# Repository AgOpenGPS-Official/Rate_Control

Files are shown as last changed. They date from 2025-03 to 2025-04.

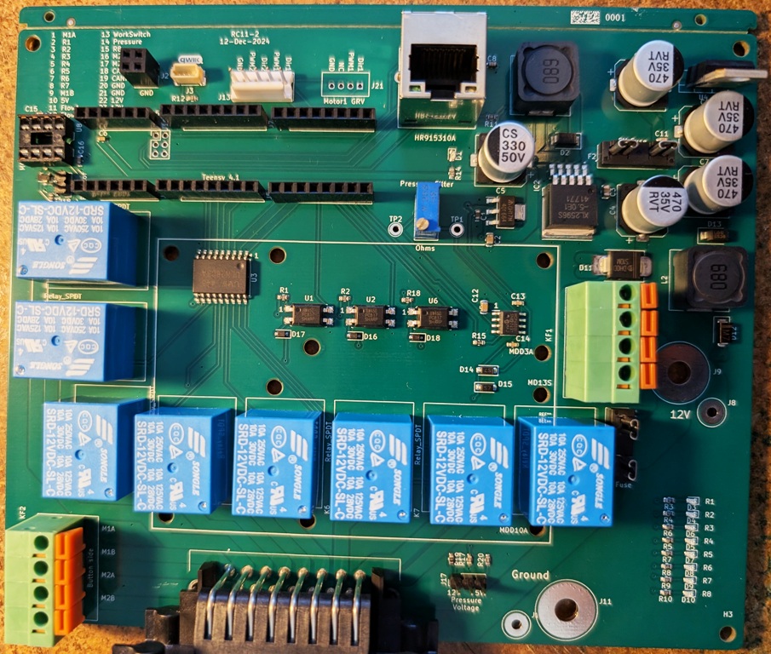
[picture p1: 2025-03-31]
Teensy/RC11-2/Bare board.jpg

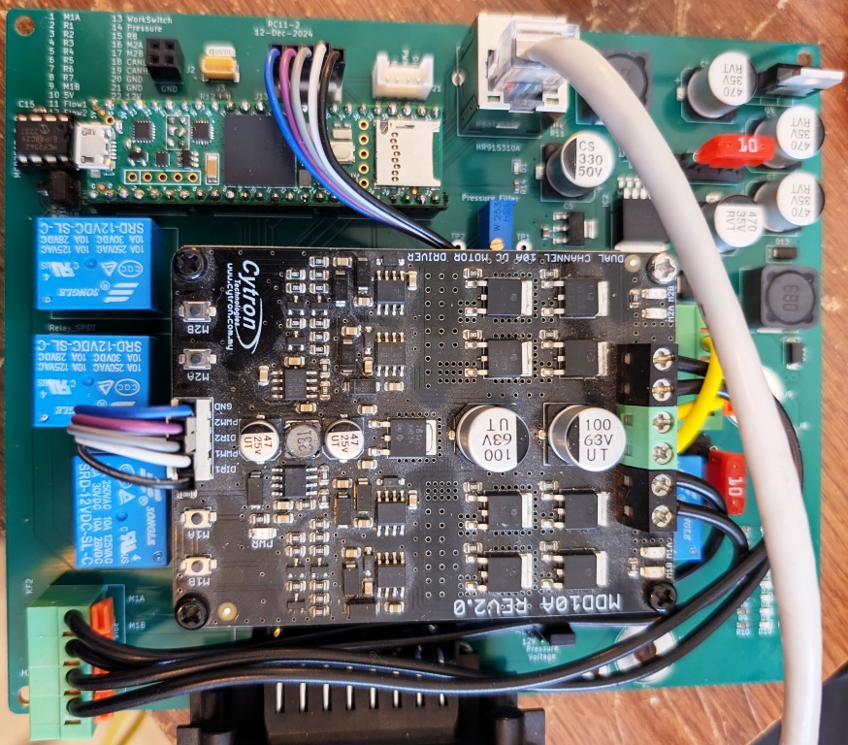
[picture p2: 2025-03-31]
Teensy/RC11-2/Dual motor drive.jpg

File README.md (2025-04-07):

### [Nano RC12-3](Nano/RC12-3)
- uses a Nano (with ENC28J60 Ethernet shield) & an on-board mounted Cytron for rate control
	- 1 or 2 [MD13S](https://www.cytron.io/p-13amp-6v-30v-dc-motor-driver) for rate control
- self assembled through-hole board, least expensive
- controls two rates
- can be connected to a relay module with a 20 pin cable or dupont connectors
- work switch
- pressure switch
- [OSHPARK]([https://oshpark.com/shared_projects/UU8e90h9](https://oshpark.com/shared_projects/fRBlR1Se)
RC12-3

#
### [Teensy 4.1 RC11-2](Teensy/RC11-2_PCB)
- uses a Teensy & an on-board mounted Cytron for rate control
	- either (1) [MD13S](https://www.cytron.io/p-13amp-6v-30v-dc-motor-driver) for single rate control
 	- or (1) [MDD10A](https://www.cytron.io/p-10amp-5v-30v-dc-motor-driver-2-channels) for dual rate control
- small components are surface mount parts
- Teensy Ethernet 
- can control two rates and eight sections
	- 8 relays (SPDT 12V output)
	- (1) 5V or 12V analog (pressure) input, potentiometer adjustable filtering
	- (2) optically isolated digital (rate/pulse) inputs (5V or 12V)
- 3.3V I2C headers (Qwiic)
	- supports optional external RelayDriver5 I2C board
 - work switch
 - canbus
RC11-2

#
### [ESP32 RC15](ESP32/RC15)
- uses an ESP32 (optional W5500 Ethernet Module)
- mostly surface mount parts
- can control two rates and 7-14 sections
	- (2) DRV8870 motor drivers with reversible outputs for rates
	- (7) DRV8870 motor drivers for either 7 reversible (motorized ball valve) outputs or 14 single ended (high or low) section outputs
- (4) 5V analog inputs (or 2 differential inputs)
- (2) optically isolated digital (rate/pulse) inputs, up to 12V
- RS485 chip & header
- 3.3V I2C header
	- supports optional external RelayDriver5 I2C board
ESP32-RC15

#
### [RelayDriver5](RelayDriver5)
- PCA9535 based I2C IO expander
- designed to plug into 8 or 16 channel relay board with Qwiic cable
RelayDriver5 photo
#
### Firmware
https://github.com/SK21/AOG_RC

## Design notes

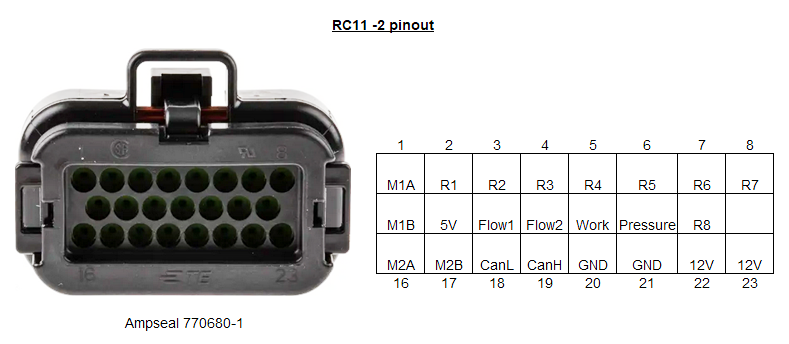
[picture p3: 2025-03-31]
Teensy/RC11-2/RC11-2 PinOut.PNG

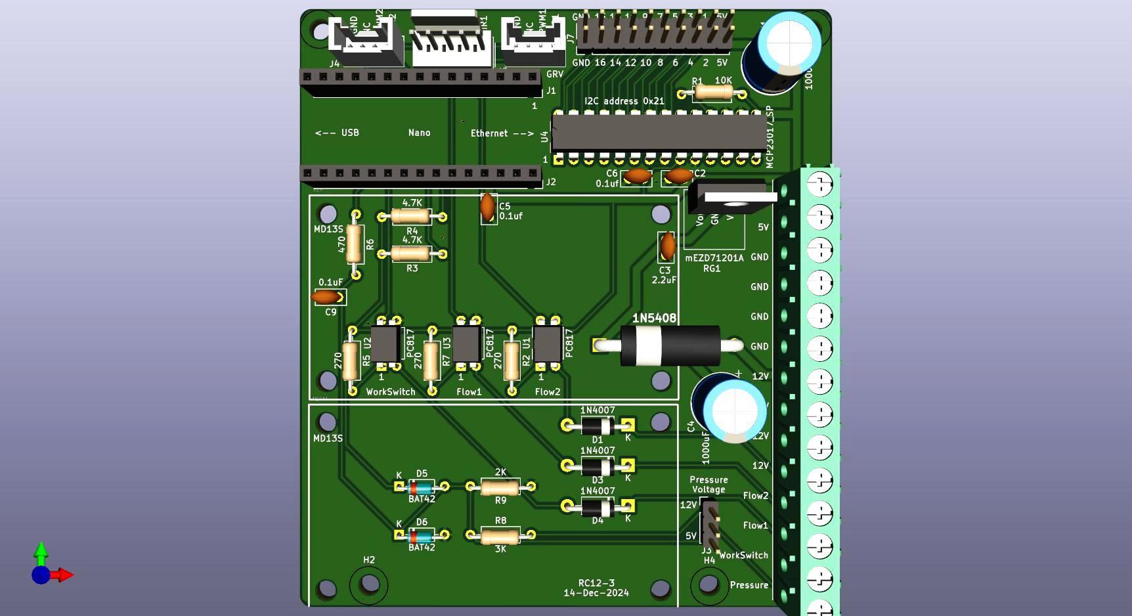
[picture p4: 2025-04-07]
Nano/RC12-3/RC12-3.jpg

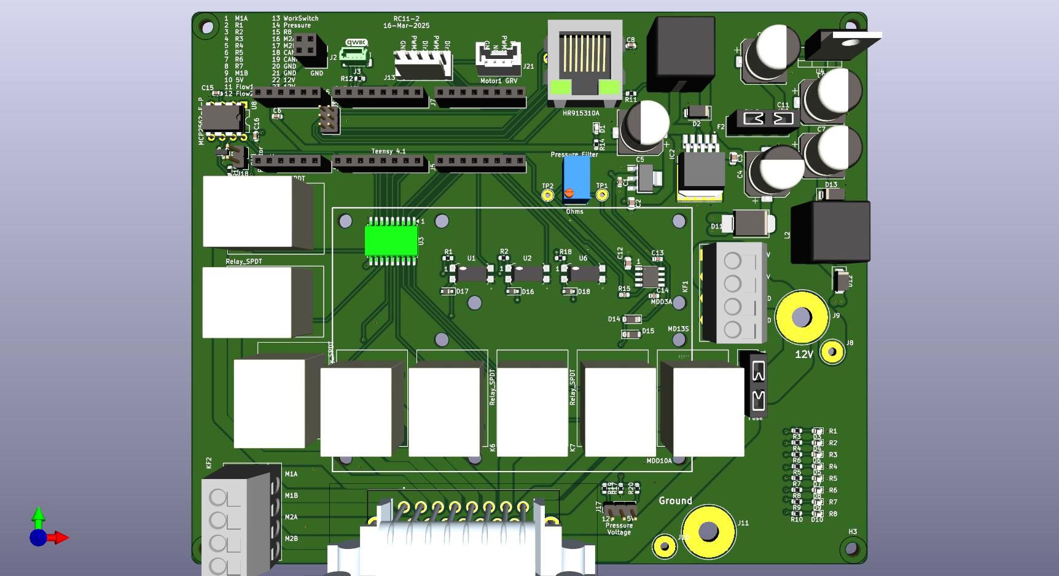
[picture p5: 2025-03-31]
Teensy/RC11-2/PCB/RC11-2.jpg

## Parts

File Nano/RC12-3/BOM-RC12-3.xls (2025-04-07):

Item # | Comment | Designator | Footprint | Quantity
1 | 1000uF | C1, C4 | CP_Radial_D10.0mm_P5.00mm | 2
2 | 10uF | C2 | C_Disc_D5.0mm_W2.5mm_P2.50mm | 1
3 | 2.2uF | C3 | C_Disc_D5.0mm_W2.5mm_P2.50mm | 1
4 | 0.1uf | C5, C6, C9 | C_Disc_D5.0mm_W2.5mm_P2.50mm | 3
5 | 1N4007 | D1, D3, D4 | D_DO-41_SOD81_P10.16mm_Horizontal | 3
6 | 1N5408 | D2 | 1N5408 | 1
7 | BAT42 | D5, D6 | D_DO-35_SOD27_P7.62mm_Horizontal | 2
8 | Conn_01x15_Female | J1, J2 | PinSocket_1x15_P2.54mm_Vertical | 2
9 | Pressure | J3 | PinHeader_1x03_P2.54mm_Vertical | 1
10 | Motor2 GRV | J4, J5 | Grove | 2
11 | Screw_Terminal_01x14 | J6 | TerminalBlock_Phoenix_PT-1,5-14-5.0-H_1x14_P5.00mm_Horizontal | 1
12 | Relay | J7 | PinHeader_2x10_P2.54mm_Vertical | 1
13 | Conn_01x05 | J9 | Molex_KK-254_AE-6410-05A_1x05_P2.54mm_Vertical | 1
14 | 10K | R1 | R_Axial_DIN0207_L6.3mm_D2.5mm_P10.16mm_Horizontal | 1
15 | 270 | R2, R5, R7 | R_Axial_DIN0207_L6.3mm_D2.5mm_P10.16mm_Horizontal | 3
16 | 4.7K | R3, R4 | R_Axial_DIN0207_L6.3mm_D2.5mm_P10.16mm_Horizontal | 2
17 | 470 | R6 | R_Axial_DIN0207_L6.3mm_D2.5mm_P10.16mm_Horizontal | 1
18 | 3K | R8 | R_Axial_DIN0207_L6.3mm_D2.5mm_P10.16mm_Horizontal | 1
19 | 2K | R9 | R_Axial_DIN0207_L6.3mm_D2.5mm_P10.16mm_Horizontal | 1
20 | mEZD71201A | RG1 | mEZD71201A | 1 | https://www.universal-solder.ca/product/dc-dc-buck-converter-5v-1a-7805-replacement/
21 | PC817 | U1, U2, U3 | DIP-4_W7.62mm | 3
22 | MCP23017_SP | U4 | DIP-28_W7.62mm | 1
23 | Nano |  |  | 1
24 | MD13S |  |  | 2
25 | IDC 20 pin flat ribbon cable |  |  | 1 | https://www.amazon.ca/Ribbon-Cable-Connector-2-54mm-Length/dp/B07T3VH9Y7
26 | 8 or 16 relay module |  |  | 1 | https://www.amazon.ca/ELEGOO-Channel-Optocoupler-Arduino-Raspberry/dp/B06XCN5JNH
27 | M3 standoffs |  |  | 4 | https://www.amazon.ca/Lystaii-Standoff-Motherboard-Standoffs-Assortment/dp/B08LPYR49C
 | RC12-3
 | Mouser # | Mfr. # | Manufacturer |  | Description | Order Qty. | Price (CAD) | Ext.: (CAD)
1 | 667-EEU-FR1E102B | EEU-FR1E102B | Panasonic |  | Aluminum Electrolytic Capacitors - Radial Leaded 25VDC 1000uF 10x20mm LS | 2 | $1.61 | $3.22
2 | 810-FA20X7S1H106KRU6 | FA20X7S1H106KRU06 | TDK |  | Multilayer Ceramic Capacitors MLCC - Leaded 50V 10uF X7S 10% RAD LS:5mm AEC-Q200 | 1 | $1.65 | $1.65
3 | 810-FG18X5R1E225KRT6 | FG18X5R1E225KRT06 | TDK |  | Multilayer Ceramic Capacitors MLCC - Leaded RAD 25V 2.2uF X5R 10% LS:2.5mm | 1 | $0.435 | $0.44
4 | 594-K104K10X7RF5UH5 | K104K10X7RF5UH5 | Vishay |  | Multilayer Ceramic Capacitors MLCC - Leaded 0.1uF 50volt 10% 5.0mm X7R | 3 | $0.261 | $0.78
5 | 637-1N4007 | 1N4007 | Diotec Semiconductor |  | Rectifiers Diode, DO-41, 1000V, 1A | 3 | $0.145 | $0.44
6 | 625-1N5408-E3 | 1N5408-E3/54 | Vishay |  | Rectifiers 3.0 Amp 1000 Volt | 1 | $0.769 | $0.77
7 | 625-BAT42 | BAT42-TR | Vishay |  | Schottky Diodes & Rectifiers 10mA 30 Volt | 2 | $0.247 | $0.49
8 | 200-SSW11501TMS | SSW-115-01-TM-S | Samtec |  | Headers & Wire Housings Tiger Buy Socket Strip with PCB Tails, .100" Pitch | 2 | $2.47 | $4.94
9 | 737-PH1-03-UA | PH1-03-UA | Adam Tech |  | Headers & Wire Housings CONN HEADER VERT 3POS 2.54MM | 1 | $0.145 | $0.15
11 | 651-1935284 | 1935284 | Phoenix Contact |  | Fixed Terminal Blocks PT 1.5/14-5.0-H | 1 | $4.29 | $4.29
12 | 737-PH2-10-UA | PH2-10-UA | Adam Tech |  | Headers & Wire Housings 10P AU FLASH SINGLE ROW STRAIGHT | 1 | $0.218 | $0.22
13 | 538-171856-0005 | 171856-0005 | Molex |  | Headers & Wire Housings KK Hdr Vrt 5 Ckt 2.54mm Pitch Sn | 1 | $0.493 | $0.49
14 | 603-CFR-12JR-5210K | CFR-12JR-52-10K | YAGEO |  | Carbon Film Resistors - Through Hole 10K ohm 1/6W 5% | 1 | $0.145 | $0.15
15 | 603-CFR-25JT-52-270R | CFR-25JT-52-270R | YAGEO |  | Carbon Film Resistors - Through Hole 1/4W 270 Ohm 5% | 3 | $0.145 | $0.44
16 | 279-CFR25J4K7 | CFR25J4K7 | TE Connectivity |  | Carbon Film Resistors - Through Hole 4.7KOhm 1/3W 1200PPM | 2 | $0.145 | $0.29
17 | 603-CFR-50JR-52470R | CFR-50JR-52-470R | YAGEO |  | Carbon Film Resistors - Through Hole 470ohm 1/2W 5% | 1 | $0.145 | $0.15
18 | 603-CFR-25JT-52-3K | CFR-25JT-52-3K | YAGEO |  | Carbon Film Resistors - Through Hole 3 kOhms 1/4W 250 V 5% - 55 C+ 155 C Axial - 350 PPM / C, + 500 PPM / C AEC-Q200 | 1 | $0.145 | $0.15
19 | 708-CF14JT2K00 | CF14JT2K00 | SEI Stackpole |  | Carbon Film Resistors - Through Hole 2KOhms 1/4W 5% Std Carbon | 1 | $0.145 | $0.15
21 | 852-PC817X3NSZ9F | PC817X3NSZ9F | Sharp Microelectronics |  | Transistor Output Optocouplers | 3 | $0.522 | $1.57
22 | 579-MCP23017-E/SP | MCP23017-E/SP | Microchip |  | Interface - I/O Expanders 16bit Input/Output Exp I2C interface | 1 | $2.45 | $2.45
24 | 713-108070021 | 108070021 | Seeed Studio |  | Power Management IC Development Tools MD13S - Cytron 13Amp DC Motor Driver | 2 | $21.03 | $42.06

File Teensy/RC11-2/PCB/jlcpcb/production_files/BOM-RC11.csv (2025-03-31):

Comment | Designator | Footprint | LCSC | Quantity
AZ1117 | IC1 | SOT230P700X180-4N | C110474 | 1
27K | RV1 | Potentiometer | C118932 | 1
0.1uF | C11,C13,C14,C15,C16,C6,C8 | C_0603_1608Metric | C14663 | 7
PESD1CAN_215 C15771 | S1 | DIO_PESD1CAN_215 | C15771 | 1
10uF | C2 | C_0805_2012Metric | C15850 | 1
I2C-3V3 | J3 | Qwic_vertical | C160390 | 1
S10MC | D11 | D_SMC_larger_pads | C169472 | 1
1N5819 C191023 | D16,D17,D18 | 1N5819 | C191023 | 3
120 | R16 | R_0603_1608Metric | C22787 | 1
150 | R11 | R_0603_1608Metric | C22808 | 1
LED | D1,D10,D3,D4,D5,D6,D7,D8,D9 | LED_0603_1608Metric | C2286 | 9
270 | R1,R18,R2 | R_0603_1608Metric | C22966 | 3
2K | R17 | R_0603_1608Metric | C22975 | 1
470 | R15 | C_0603_1608Metric | C23179 | 1
500 | R14 | R_0603_1608Metric | C23193 | 1
750 | R10,R3,R4,R5,R6,R7,R8,R9 | R_0603_1608Metric | C23253 | 8
Conn_01x08_Female | J16,J5,J6,J7 | PinSocket_1x08_P2.54mm_Vertical | C27438 | 4
HR915310A | J14 | CONN8_HR91531_HAN | C2760326 | 1
5.2K | R19 | R_0603_1608Metric | C2828621 | 1
1uF | C12,C3 | C_0805_2012Metric | C28323 | 2
470uF | C10,C4,C7,C9 | CP_Elec_10x10.5 | C2836436 | 4
SS36 | D13,D2 | SMA(DO-214AC) | C2903825 | 2
1K | R20 | R_0603_1608Metric | C2907113 | 1
Pressure | J17 | PinHeader_1x03_P2.54mm_Vertical | C2937625 | 1
Conn_02x02_Counter_Clockwise | J2 | PinSocket_2x02_P2.54mm_Vertical | C2977590 | 1
Relay_SPDT | K1,K2,K3,K4,K5,K6,K7,K8 | Songle_SRD-05VDC-SL-C | C30431 | 8
MCP2562-E-P | U8 | DIP-8_W7.62mm | C305904 | 1
776087-1-776087-1 | J12 | 7760871 | C378893 | 1
Motor1 GRV | J21 | Grove | C403774 | 1
Conn_01x06_Female | J15,J4 | PinSocket_1x06_P2.54mm_Vertical | C40877 | 2
2.2K | R12,R13 | R_0603_1608Metric | C4190 | 2
KF142V-5.0-4P | KF1,KF2 | KF142V-5.08-4P | C475136 | 2
Can Resistor | J18 | PinHeader_1x02_P2.54mm_Vertical | C492401 | 1
C492610 | F1,F2 | Fuse_Holder_C492610 | C492610 | 2
330uF | C5 | CP_Elec_10x10.5 | C5162354 | 1
LM7805_TO220 | U4 | TO-220-3_Vertical | C5444281 | 1
BAT42 | D14,D15 | D_SOD-123 | C5805639 | 2
22uF | C1 | C_0603_1608Metric | C59461 | 1
PC817 C66405 | U1,U2,U6 | SMD-4_4.6x7.62mm_P2.54mm | C66405 | 3
1N4007 C727081 | D12 | SMA(DO-214AC) | C727081 | 1
MCP6002-xP | U5 | SOIC127P600X175-8N | C7377 | 1
XL2596 | IC2 | TO263-5L | C74190 | 1
ULN2803A | U3 | ULN2803A | C845537 | 1
Conn_01x05 | J13 | Molex_KK-254_AE-6410-05A_1x05_P2.54mm_Vertical | C86505 | 1
SMDRI127-680MT | L1,L2 | TMPA1265SP-101MN-D | C9907 | 2
12V | J8 | PowerPinSmall |  | 1
Ground | J11 | PowerPin |  | 1
12V | J9 | PowerPin |  | 1
Ground | J10 | PowerPinSmall |  | 1
Pressure Ohms1 | TP1 | TestPoint_THTPad_D2.5mm_Drill1.2mm |  | 1
Pressure Ohms2 | TP2 | TestPoint_THTPad_D2.5mm_Drill1.2mm |  | 1
Teensy_Ethernet | J1 | PinHeader_2x03_P2.00mm_Vertical |  | 1

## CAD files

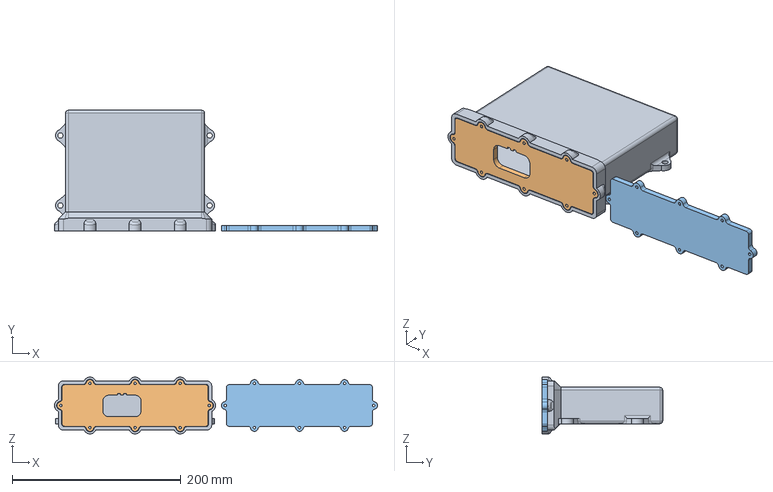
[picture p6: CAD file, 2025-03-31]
Teensy/RC11-2/Enclosure/RC11 box v7.step
383.1 x 143.0 x 67.4 mm

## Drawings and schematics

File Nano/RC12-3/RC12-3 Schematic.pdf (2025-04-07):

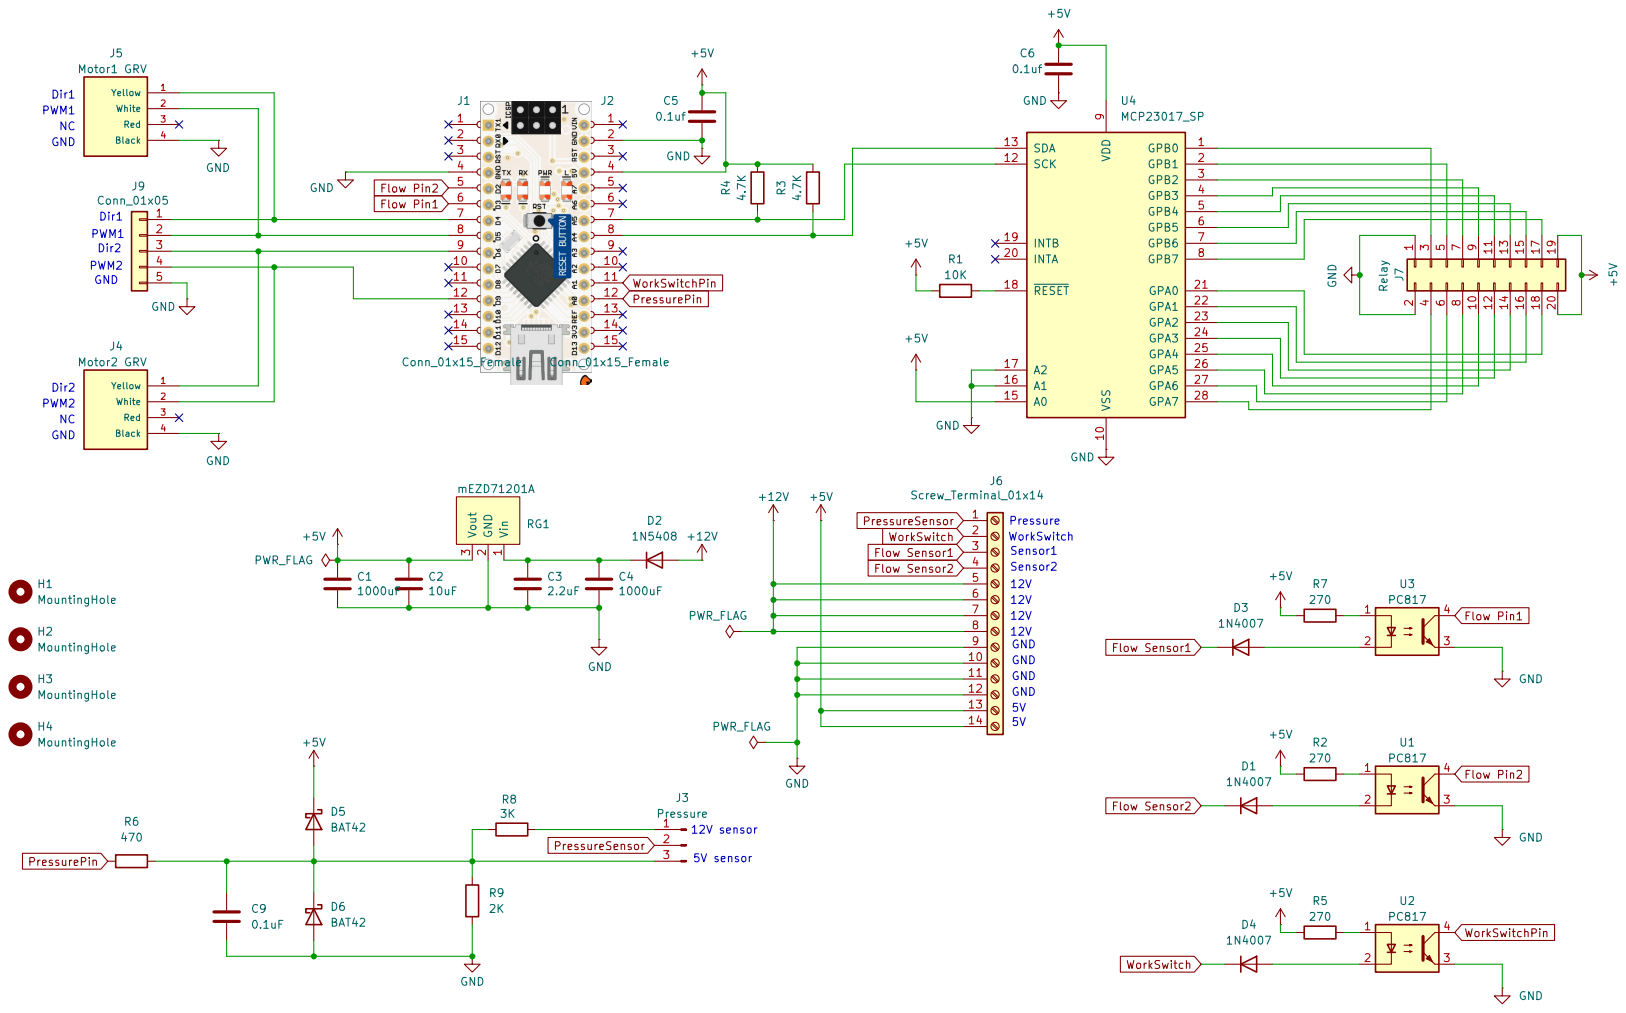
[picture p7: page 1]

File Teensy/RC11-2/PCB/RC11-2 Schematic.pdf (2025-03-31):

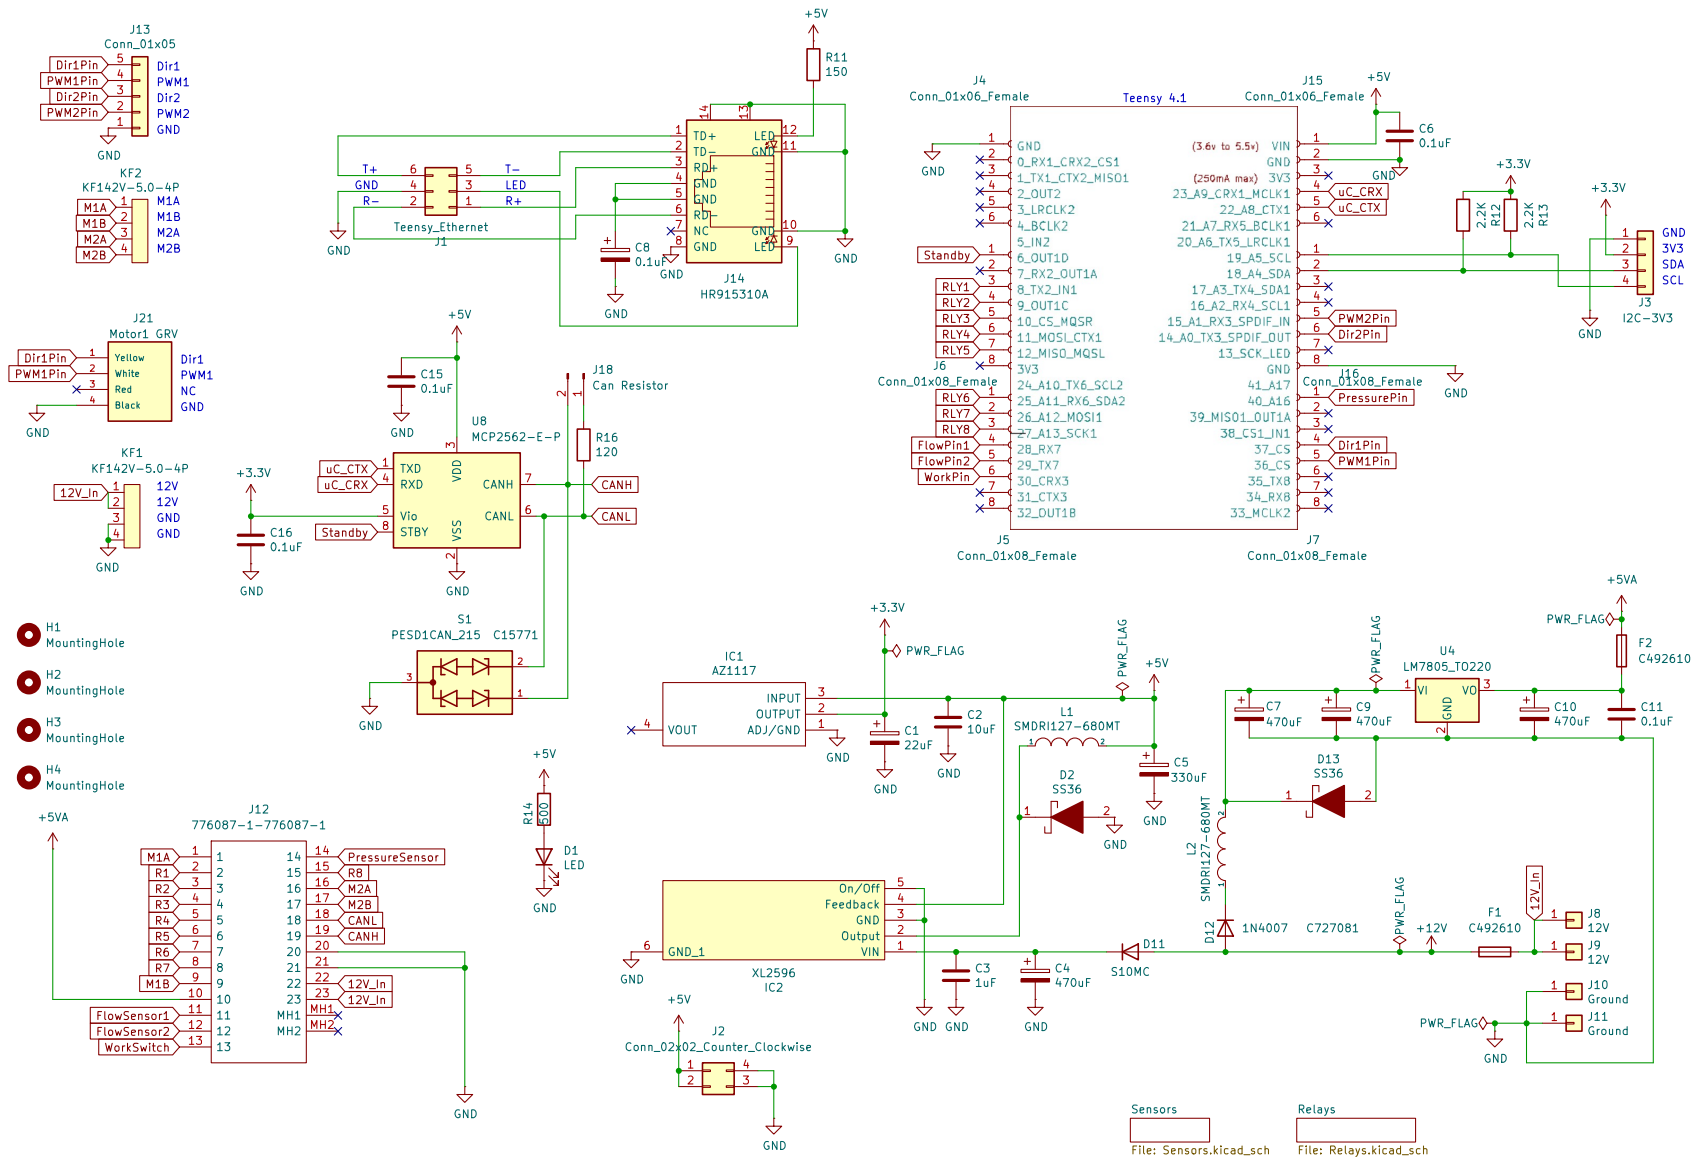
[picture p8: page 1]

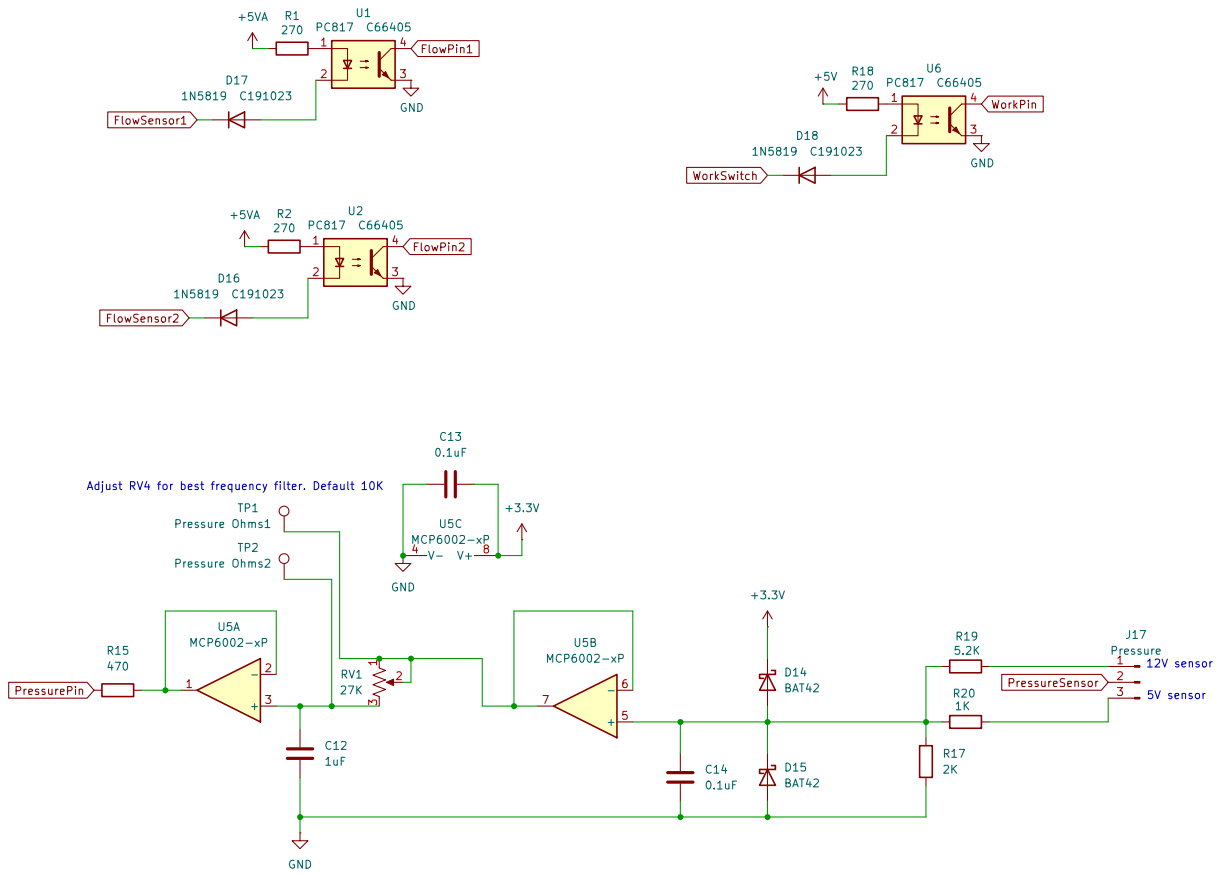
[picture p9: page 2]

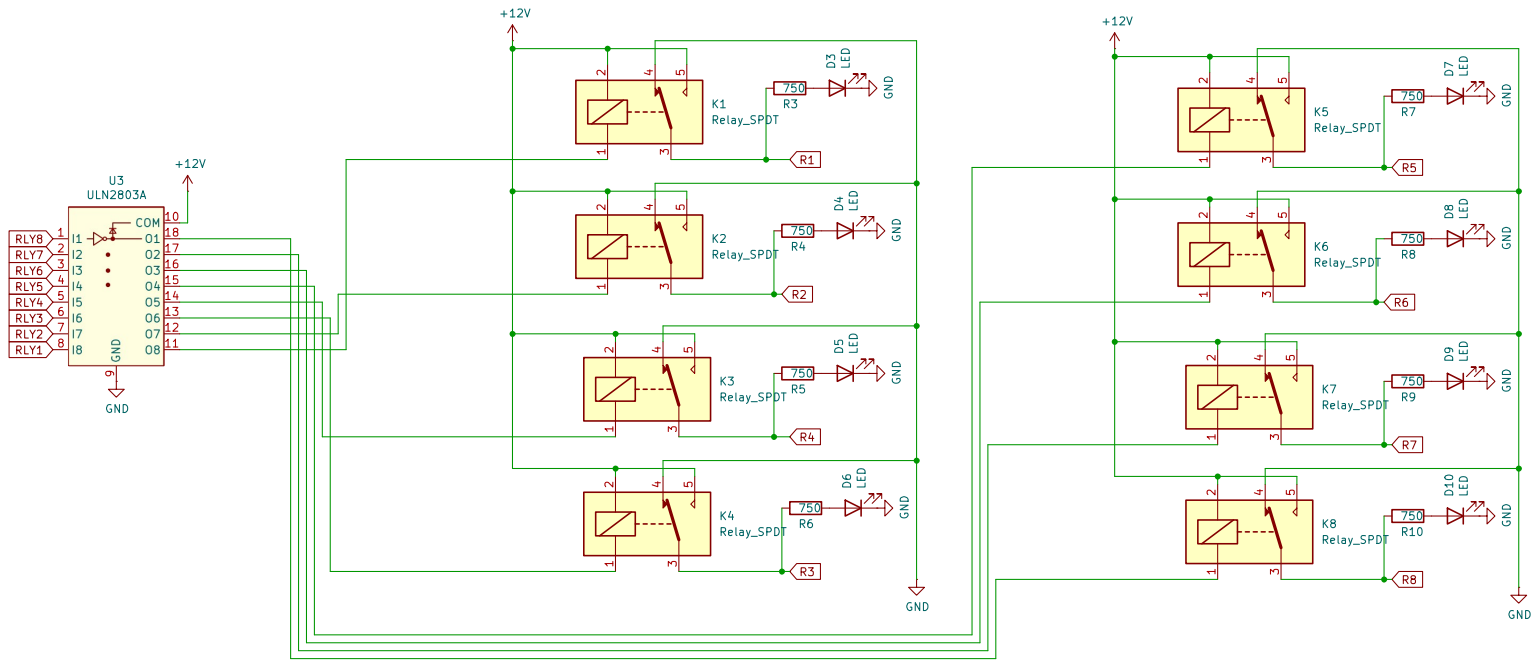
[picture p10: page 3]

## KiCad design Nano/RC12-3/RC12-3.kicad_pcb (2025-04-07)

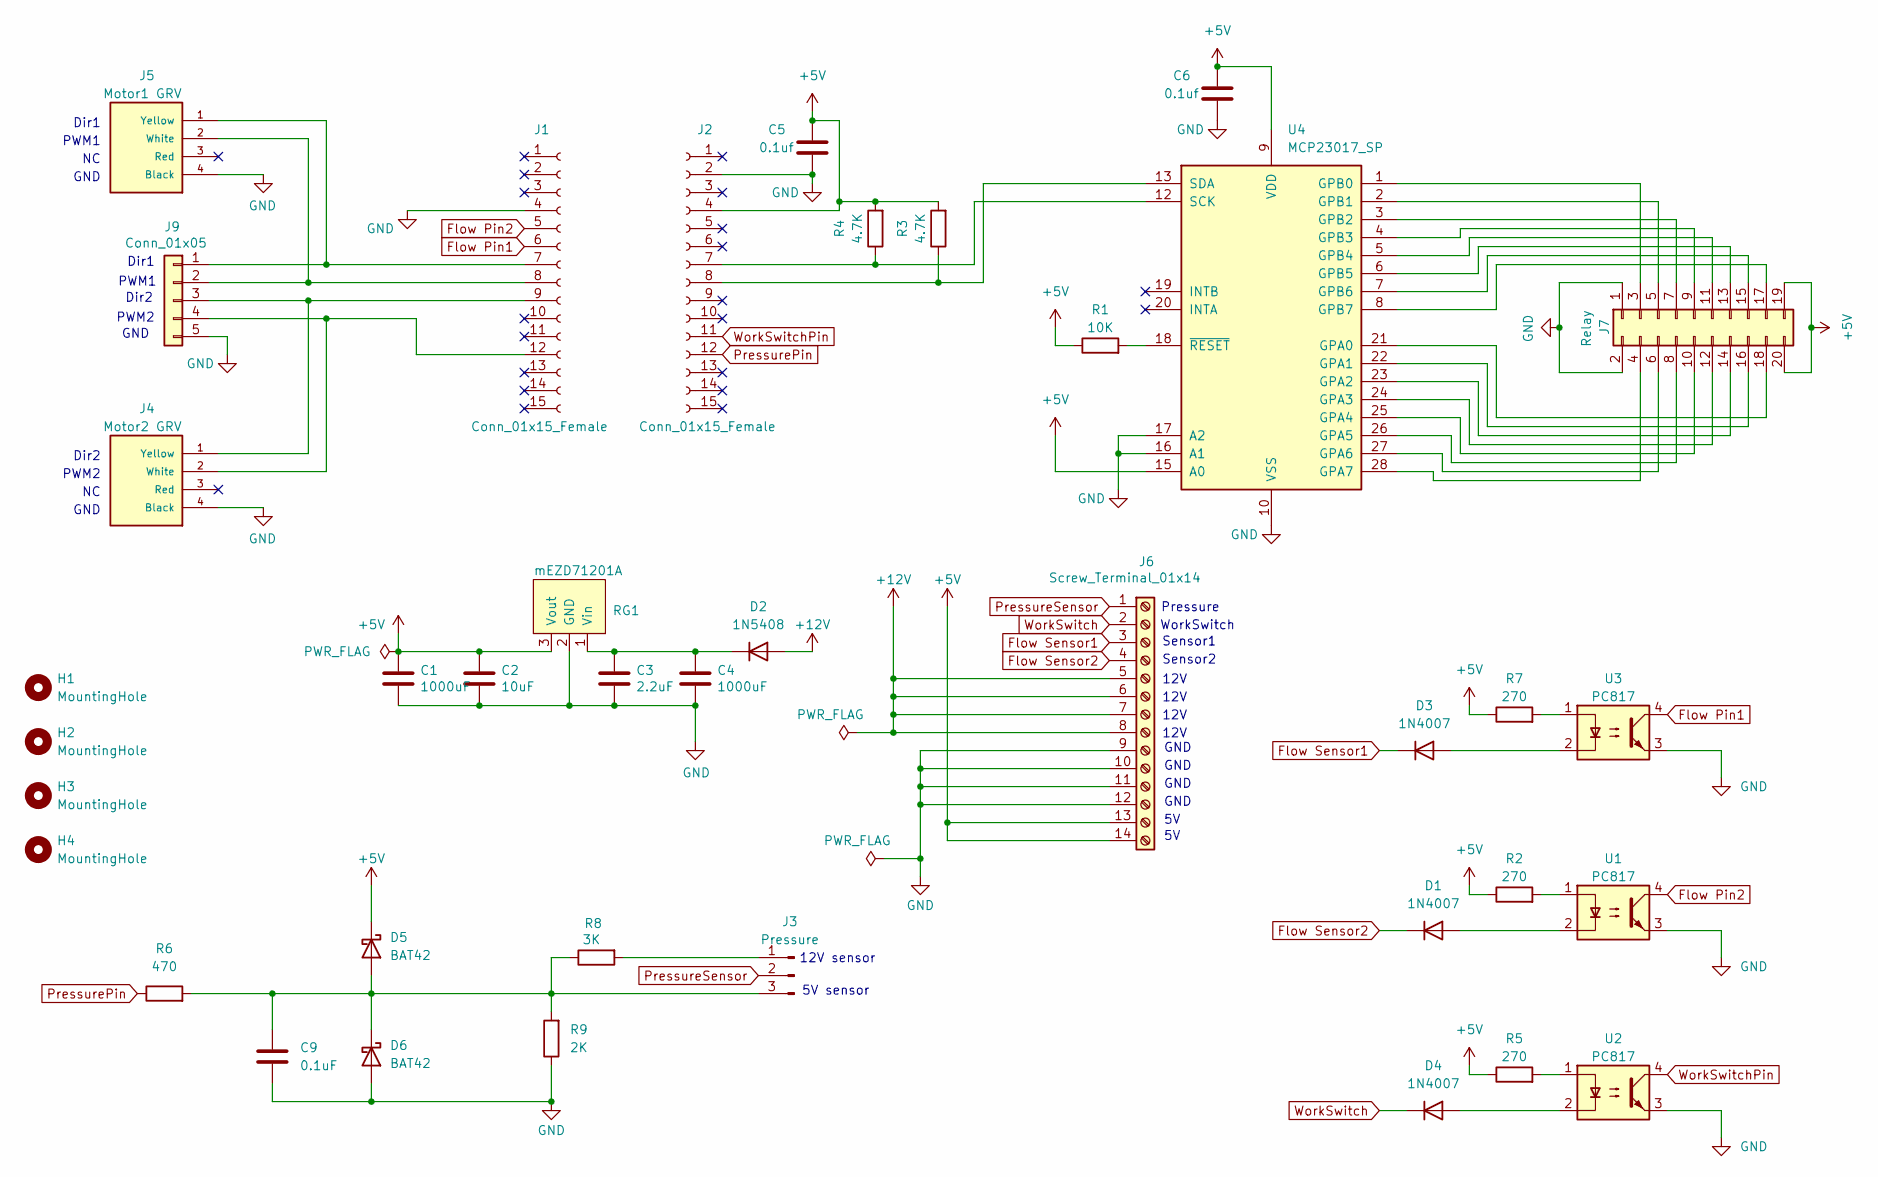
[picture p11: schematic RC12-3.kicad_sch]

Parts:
C1, C4: 1000uF; CP_Radial_D10.0mm_P5.00mm
C2: 10uF; C_Disc_D5.0mm_W2.5mm_P2.50mm
C3: 2.2uF; C_Disc_D5.0mm_W2.5mm_P2.50mm
C5, C6: 0.1uf; C_Disc_D5.0mm_W2.5mm_P2.50mm
C9: 0.1uF; C_Disc_D5.0mm_W2.5mm_P2.50mm
D1, D3, D4: 1N4007; D_DO-41_SOD81_P10.16mm_Horizontal
D2: 1N5408
D5, D6: BAT42; D_DO-35_SOD27_P7.62mm_Horizontal
H1, H2, H3, H4: MountingHole; MountingHole_3.2mm_M3
J1, J2: Conn_01x15_Female; PinSocket_1x15_P2.54mm_Vertical
J3: Pressure; PinHeader_1x03_P2.54mm_Vertical
J4: Motor2 GRV; Grove
J5: Motor1 GRV; Grove
J6: Screw_Terminal_01x14; TerminalBlock_Phoenix_PT-1,5-14-5.0-H_1x14_P5.00mm_Horizont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
J7: Relay; PinHeader_2x10_P2.54mm_Vertical
J9: Conn_01x05; Molex_KK-254_AE-6410-05A_1x05_P2.54mm_Vertical
R1: 10K; R_Axial_DIN0207_L6.3mm_D2.5mm_P10.16mm_Horizontal
R2, R5, R7: 270; R_Axial_DIN0207_L6.3mm_D2.5mm_P10.16mm_Horizontal
R3, R4: 4.7K; R_Axial_DIN0207_L6.3mm_D2.5mm_P10.16mm_Horizontal
R6: 470; R_Axial_DIN0207_L6.3mm_D2.5mm_P10.16mm_Horizontal
R8: 3K; R_Axial_DIN0207_L6.3mm_D2.5mm_P10.16mm_Horizontal
R9: 2K; R_Axial_DIN0207_L6.3mm_D2.5mm_P10.16mm_Horizontal
RG1: mEZD71201A
U1, U2, U3: PC817; DIP-4_W7.62mm
U4: MCP23017_SP; DIP-28_W7.62mm

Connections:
+5V: C1.1, C2.1, C5.2, C6.2, D5.1 (K), J2.4, J6.13, J6.14, J7.19, J7.20, R1.1, R2.1, R3.2, R4.2, R5.1, R7.1, RG1.3 (Vout), U4.9 (VDD), U4.15 (A0)
+12V: D2.2 (A), J6.5, J6.6, J6.7, J6.8
Flow Pin1: J1.6, U3.4
Flow Pin2: J1.5, U1.4
Flow Sensor1: D3.1 (K), J6.3
Flow Sensor2: D1.1 (K), J6.4
GND: C1.2, C2.2, C3.2, C4.2, C5.1, C6.1, C9.2, D6.2 (A), J1.4, J2.2, J4.4 (Black), J5.4 (Black), J6.9, J6.10, J6.11, J6.12, J7.1, J7.2, J9.5, R9.1, RG1.2 (GND), U1.3, U2.3, U3.3, U4.10 (VSS), U4.16 (A1), U4.17 (A2)
unnamed: D1.2 (A), U1.2
unnamed: C3.1, C4.1, D2.1 (K), RG1.1 (Vin)
unnamed: D3.2 (A), U3.2
unnamed: D4.2 (A), U2.2
unnamed: C9.1, D5.2 (A), D6.1 (K), J3.3, R6.2, R8.1, R9.2
unnamed: J1.7, J5.1 (Yellow), J9.1
unnamed: J1.8, J5.2 (White), J9.2
unnamed: J1.9, J4.1 (Yellow), J9.3
unnamed: J1.12, J4.2 (White), J9.4
unnamed: J2.7, R4.1, U4.12 (SCK)
unnamed: J2.8, R3.1, U4.13 (SDA)
unnamed: J3.1, R8.2
unnamed: J7.3, U4.1 (GPB0)
unnamed: J7.4, U4.28 (GPA7)
unnamed: J7.5, U4.2 (GPB1)
unnamed: J7.6, U4.27 (GPA6)
unnamed: J7.7, U4.3 (GPB2)
unnamed: J7.8, U4.26 (GPA5)
unnamed: J7.9, U4.4 (GPB3)
unnamed: J7.10, U4.25 (GPA4)
unnamed: J7.11, U4.5 (GPB4)
unnamed: J7.12, U4.24 (GPA3)
unnamed: J7.13, U4.6 (GPB5)
unnamed: J7.14, U4.23 (GPA2)
unnamed: J7.15, U4.7 (GPB6)
unnamed: J7.16, U4.22 (GPA1)
unnamed: J7.17, U4.8 (GPB7)
unnamed: J7.18, U4.21 (GPA0)
unnamed: R2.2, U1.1
unnamed: R5.2, U2.1
unnamed: R7.2, U3.1
unnamed: R1.2, U4.18 (~RESET)
PressurePin: J2.12, R6.1
PressureSensor: J3.2, J6.1
WorkSwitch: D4.1 (K), J6.2
WorkSwitchPin: J2.11, U2.4

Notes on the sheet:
Pressure
GND
PWM1
12V
WorkSwitch
PWM2
Dir1
12V sensor
Dir2
Dir2
5V sensor
Sensor1
Sensor2

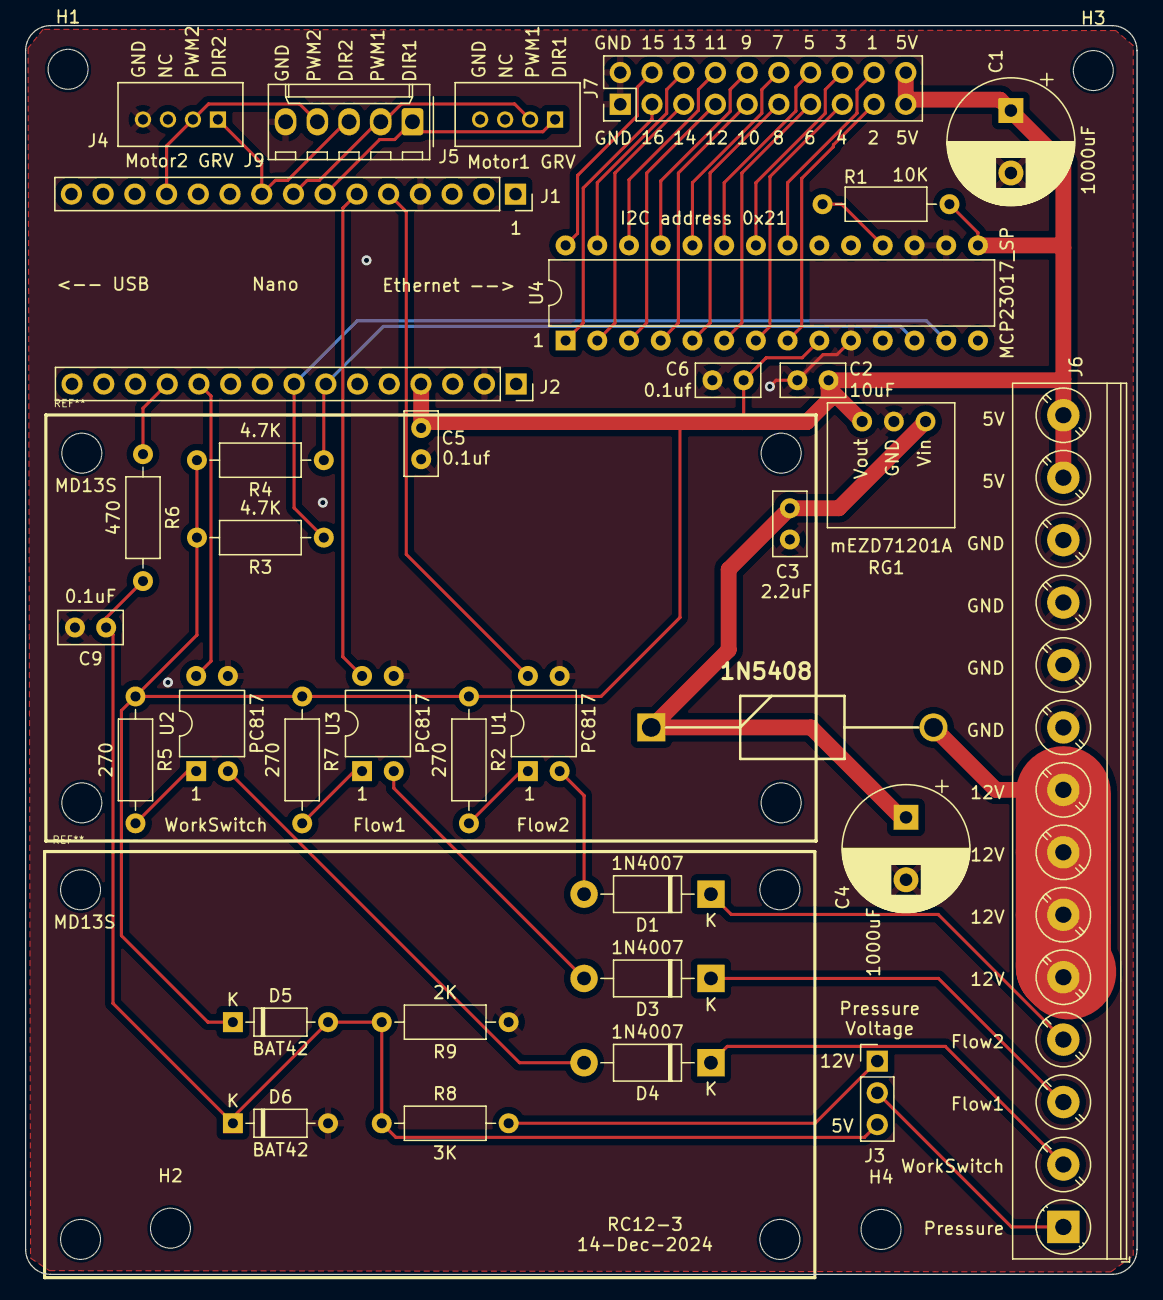
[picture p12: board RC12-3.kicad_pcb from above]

Board: 2 copper layers, 89.0 x 100.0 mm, 39 parts (0 on the bottom side), 43 nets.

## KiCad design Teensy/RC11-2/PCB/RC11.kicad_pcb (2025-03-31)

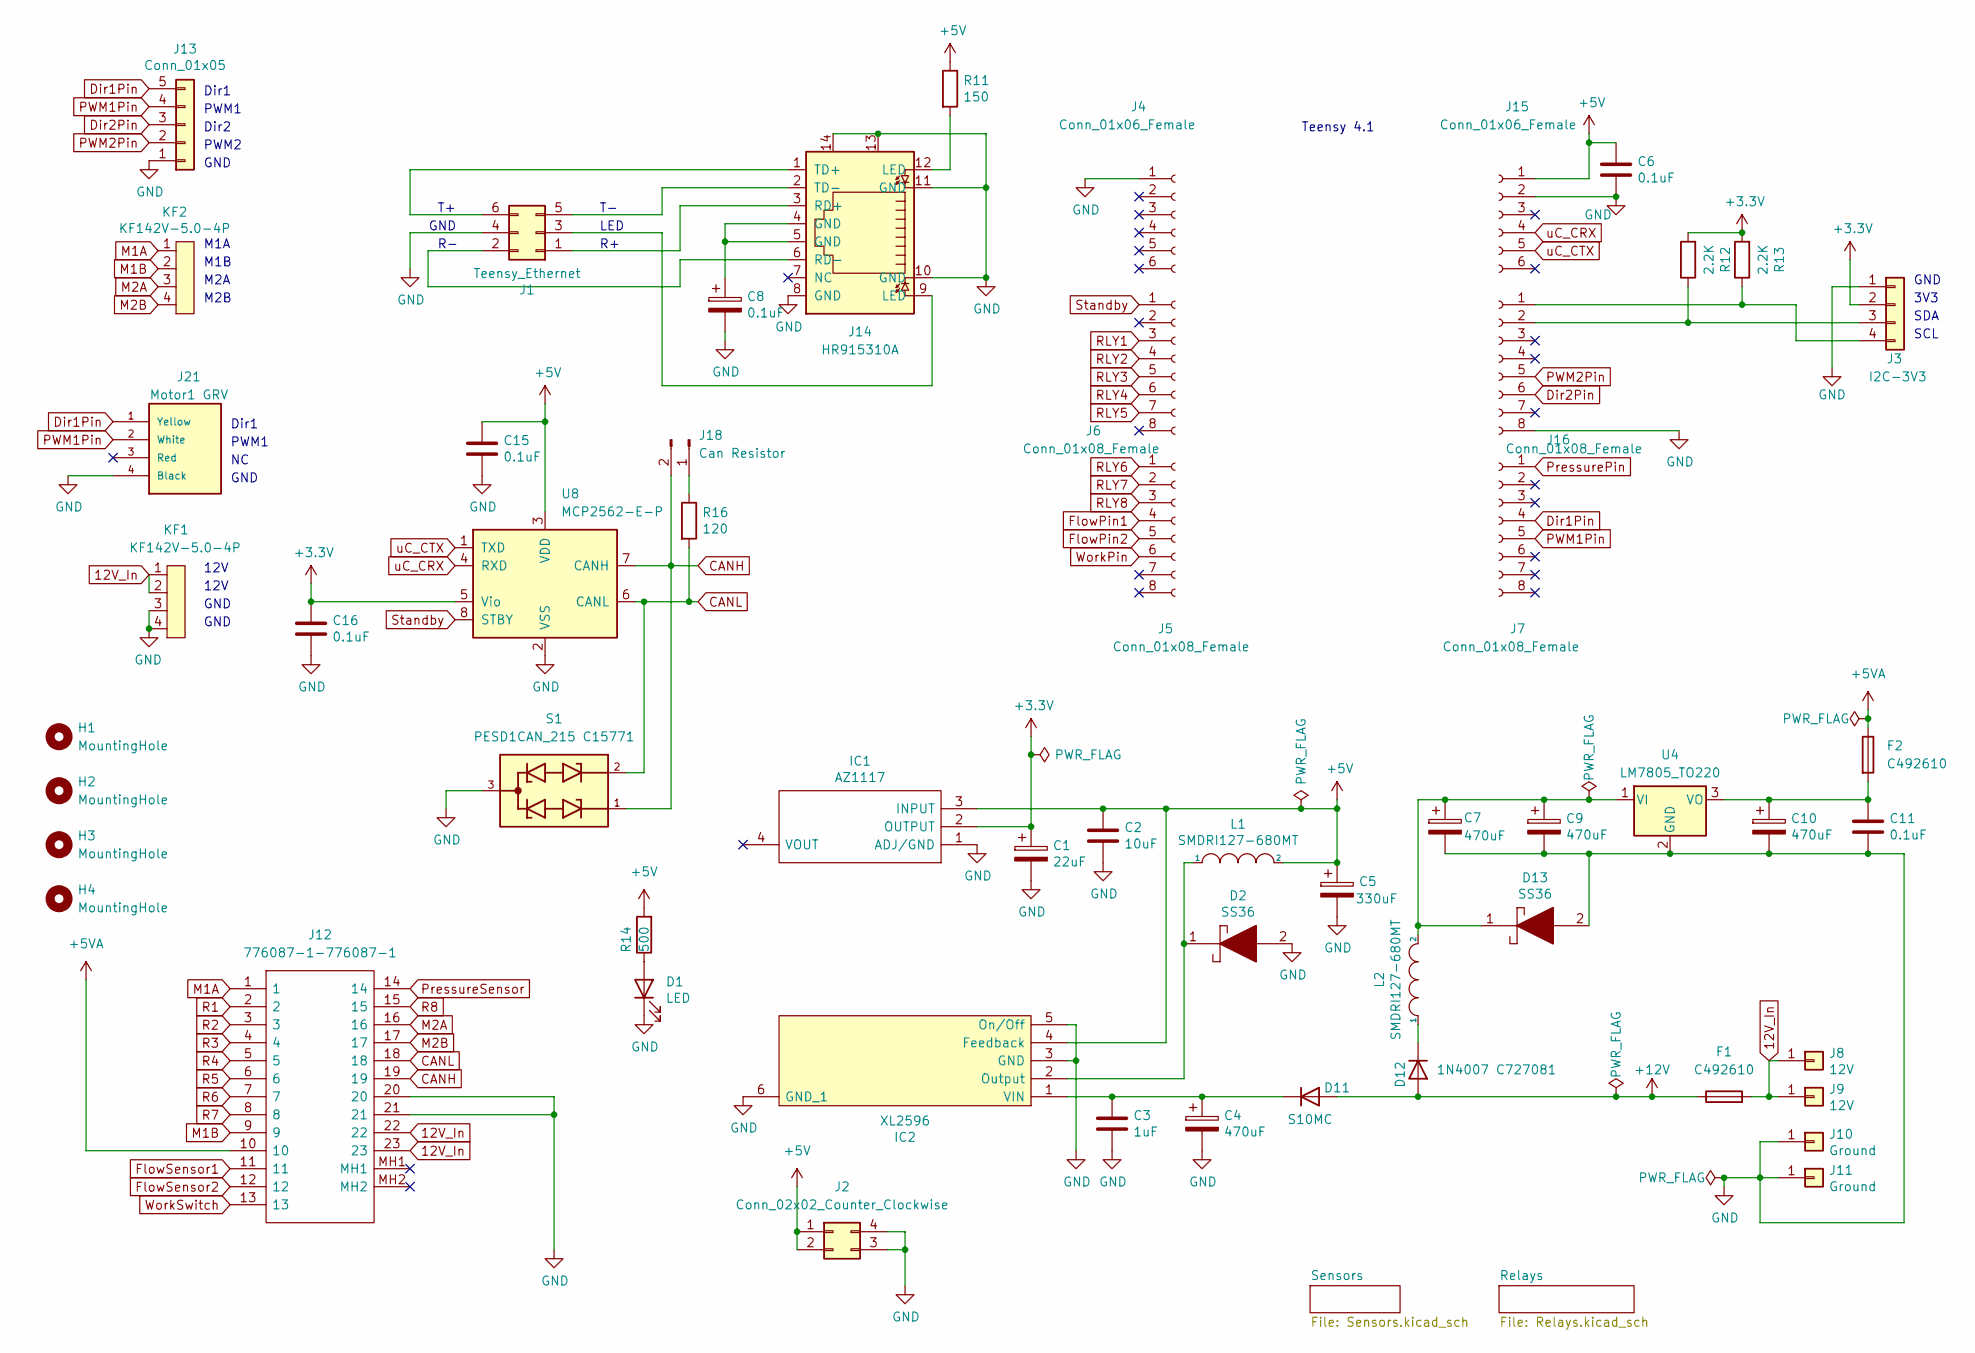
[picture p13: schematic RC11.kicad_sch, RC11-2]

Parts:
C1: 22uF; C_0603_1608Metric
C2: 10uF; C_0805_2012Metric
C3: 1uF; C_0805_2012Metric
C4, C7, C9, C10: 470uF; CP_Elec_10x10.5
C5: 330uF; CP_Elec_10x10.5
C6, C8, C11, C15, C16: 0.1uF; C_0603_1608Metric
D1: LED; LED_0603_1608Metric
D2, D13: SS36; SMA(DO-214AC)
D11: S10MC; D_SMC_larger_pads
D12: 1N4007 C727081; SMA(DO-214AC)
F1, F2: C492610; Fuse_Holder_C492610
H1, H2, H3, H4: MountingHole; MountingHole_3.2mm_M3
IC1: AZ1117; SOT230P700X180-4N; Mouser Part Number 621-AZ1117CH-3.3TRG1
IC2: XL2596; TO263-5L
J1: Teensy_Ethernet; PinHeader_2x03_P2.00mm_Vertical
J2: Conn_02x02_Counter_Clockwise; PinSocket_2x02_P2.54mm_Vertical
J3: I2C-3V3; Qwic_vertical
J4, J15: Conn_01x06_Female; PinSocket_1x06_P2.54mm_Vertical
J5, J6, J7, J16: Conn_01x08_Female; PinSocket_1x08_P2.54mm_Vertical
J8: 12V; PowerPinSmall
J9: 12V; PowerPin
J10: Ground; PowerPinSmall
J11: Ground; PowerPin
J12: 776087-1-776087-1; 7760871; Mouser Part Number 571-776087-1
J13: Conn_01x05; Molex_KK-254_AE-6410-05A_1x05_P2.54mm_Vertical
J14: HR915310A; CONN8_HR91531_HAN
J18: Can Resistor; PinHeader_1x02_P2.54mm_Vertical
J21: Motor1 GRV; Grove
KF1, KF2: KF142V-5.0-4P; KF142V-5.08-4P
L1, L2: SMDRI127-680MT; TMPA1265SP-101MN-D
R11: 150; R_0603_1608Metric
R12, R13: 2.2K; R_0603_1608Metric
R14: 500; R_0603_1608Metric
R16: 120; R_0603_1608Metric
S1: PESD1CAN_215 C15771; DIO_PESD1CAN_215
U4: LM7805_TO220; TO-220-3_Vertical
U8: MCP2562-E-P; DIP-8_W7.62mm

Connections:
12V_In: F1.2, J8.1, J9.1, J12.22, J12.23, KF1.1, KF1.2
+3.3V: C1.1, C16.1, IC1.2 (OUTPUT), J3.2, R12.2, R13.2, U8.5 (Vio); also elsewhere on the board
+5V: C2.1, C5.1, C6.1, C15.1, IC1.3 (INPUT), IC2.4 (Feedback), J2.1, J2.2, J15.1, L1.2, R11.1, R14.2, U8.3 (VDD); also elsewhere on the board
+5VA: F2.1, J12.10; also elsewhere on the board
+12V: D11.2 (A), D12.2 (A), F1.1; also elsewhere on the board
CANH: J12.19, J18.2, S1.1, U8.7 (CANH)
CANL: J12.18, R16.2, S1.2, U8.6 (CANL)
Dir1Pin: J7.4, J13.5, J21.1 (Yellow)
Dir2Pin: J13.3, J16.6
FlowPin1: J5.4; also elsewhere on the board
FlowPin2: J5.5; also elsewhere on the board
FlowSensor1: J12.11; also elsewhere on the board
FlowSensor2: J12.12; also elsewhere on the board
GND: C1.2, C2.2, C3.2, C4.2, C5.2, C6.2, C7.2, C8.2, C9.2, C10.2, C11.2, C15.2, C16.2, D1.1 (K), D2.2, D13.2, IC1.1 (ADJ/GND), IC2.3 (GND), IC2.5 (On/Off), IC2.6 (GND_1), J1.4, J2.3, J2.4, J3.1, J4.1, J10.1, J11.1, J12.20, J12.21, J13.1, J14.8 (GND), J14.10 (GND), J14.11 (GND), J14.13, J14.14, J15.2, J16.8, J21.4 (Black), KF1.3, KF1.4, S1.3, U4.2 (GND), U8.2 (VSS); also elsewhere on the board
M1A: J12.1, KF2.1
M1B: J12.9, KF2.2
M2A: J12.16, KF2.3
M2B: J12.17, KF2.4
unnamed: C8.1, J14.4 (GND), J14.5 (GND)
unnamed: D1.2 (A), R14.1
unnamed: C3.1, C4.1, D11.1 (K), IC2.1 (VIN)
unnamed: D12.1 (K), L2.1
unnamed: D2.1, IC2.2 (Output), L1.1
unnamed: J1.1, J14.3 (RD+)
unnamed: J1.2, J14.6 (RD-)
unnamed: J1.3, J14.9 (LED)
unnamed: J1.5, J14.2 (TD-)
unnamed: J1.6, J14.1 (TD+)
unnamed: J14.12 (LED), R11.2
unnamed: J3.4, J16.1, R13.1
unnamed: J3.3, J16.2, R12.1
unnamed: J18.1, R16.1
unnamed: C7.1, C9.1, D13.1, L2.2, U4.1 (VI)
unnamed: C10.1, C11.1, F2.2, U4.3 (VO)
PWM1Pin: J7.5, J13.4, J21.2 (White)
PWM2Pin: J13.2, J16.5
PressurePin: J7.1; also elsewhere on the board
PressureSensor: J12.14; also elsewhere on the board
R1: J12.2; also elsewhere on the board
R2: J12.3; also elsewhere on the board
R3: J12.4; also elsewhere on the board
R4: J12.5; also elsewhere on the board
R5: J12.6; also elsewhere on the board
R6: J12.7; also elsewhere on the board
R7: J12.8; also elsewhere on the board
R8: J12.15; also elsewhere on the board
RLY1: J6.3; also elsewhere on the board
RLY2: J6.4; also elsewhere on the board
RLY3: J6.5; also elsewhere on the board
RLY4: J6.6; also elsewhere on the board
RLY5: J6.7; also elsewhere on the board
RLY6: J5.1; also elsewhere on the board
RLY7: J5.2; also elsewhere on the board
RLY8: J5.3; also elsewhere on the board
Standby: J6.1, U8.8 (STBY)
WorkPin: J5.6; also elsewhere on the board
WorkSwitch: J12.13; also elsewhere on the board
uC_CRX: J15.4, U8.4 (RXD)
uC_CTX: J15.5, U8.1 (TXD)

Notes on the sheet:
GND
Dir2
Dir1
M2A
PWM1
PWM1
M1B
M2B
SCL
LED
Teensy 4.1
PWM2
12V
SDA
M1A
3V3

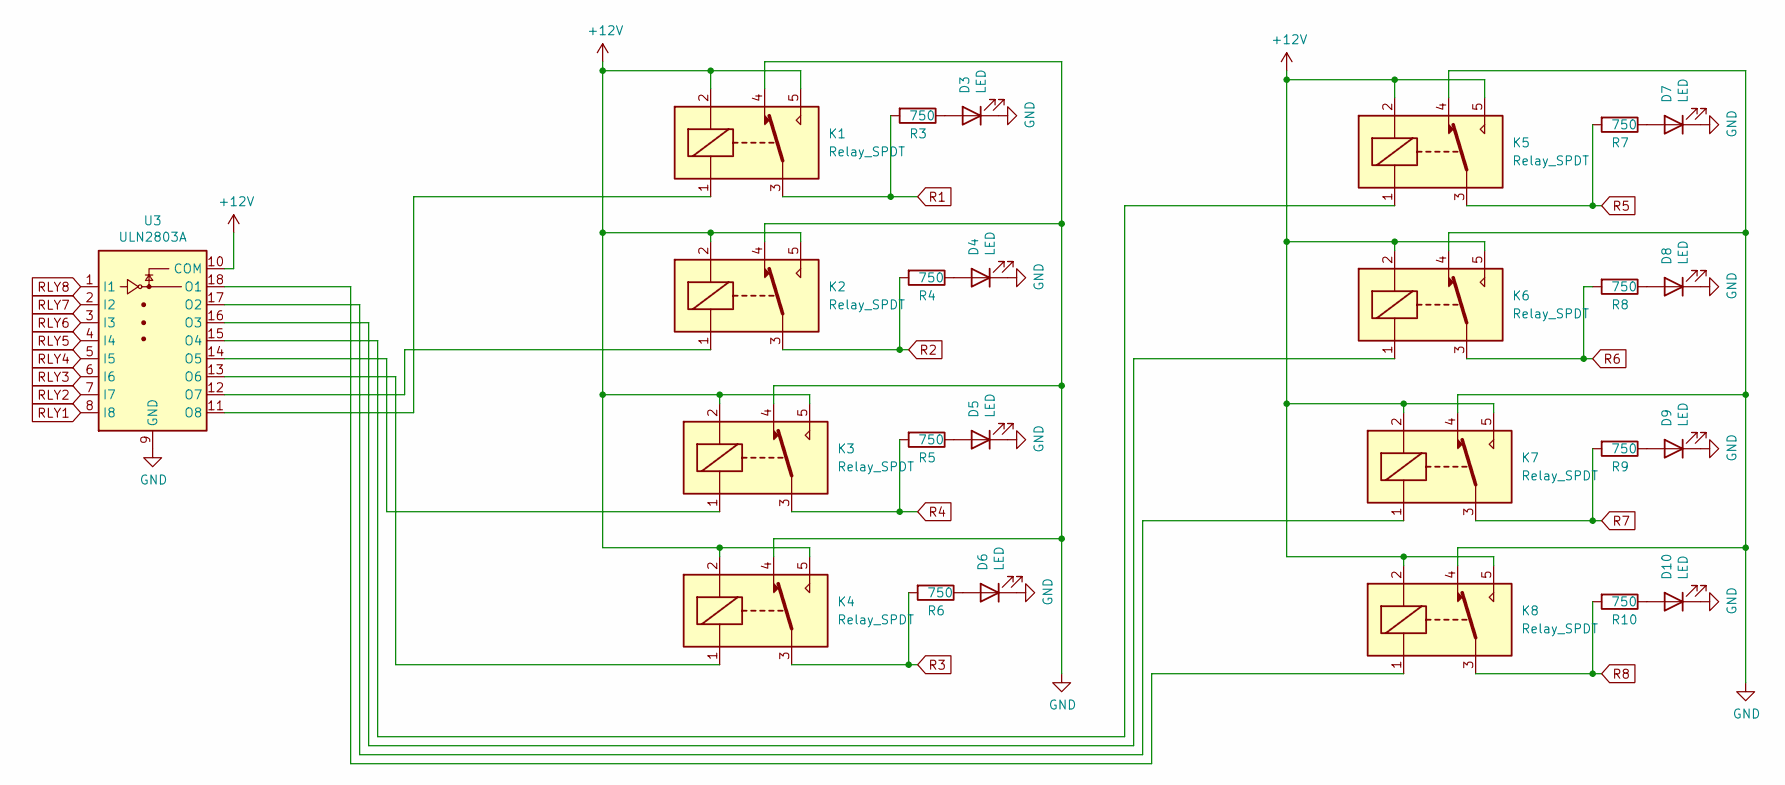
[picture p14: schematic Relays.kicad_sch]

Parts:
D3, D4, D5, D6, D7, D8, D9, D10: LED; LED_0603_1608Metric
K1, K2, K3, K4, K5, K6, K7, K8: Relay_SPDT; Songle_SRD-05VDC-SL-C
R3, R4, R5, R6, R7, R8, R9, R10: 750; R_0603_1608Metric
U3: ULN2803A

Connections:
+12V: K1.2, K1.5, K2.2, K2.5, K3.2, K3.5, K4.2, K4.5, K5.2, K5.5, K6.2, K6.5, K7.2, K7.5, K8.2, K8.5, U3.10 (COM); also elsewhere on the board
GND: D3.1 (K), D4.1 (K), D5.1 (K), D6.1 (K), D7.1 (K), D8.1 (K), D9.1 (K), D10.1 (K), K1.4, K2.4, K3.4, K4.4, K5.4, K6.4, K7.4, K8.4, U3.9 (GND); also elsewhere on the board
unnamed: D3.2 (A), R3.1
unnamed: D4.2 (A), R4.1
unnamed: D5.2 (A), R5.1
unnamed: D6.2 (A), R6.1
unnamed: D7.2 (A), R7.1
unnamed: D8.2 (A), R8.1
unnamed: D9.2 (A), R9.1
unnamed: D10.2 (A), R10.1
unnamed: K8.1, U3.18 (O1)
unnamed: K7.1, U3.17 (O2)
unnamed: K6.1, U3.16 (O3)
unnamed: K5.1, U3.15 (O4)
unnamed: K3.1, U3.14 (O5)
unnamed: K4.1, U3.13 (O6)
unnamed: K2.1, U3.12 (O7)
unnamed: K1.1, U3.11 (O8)
R1: K1.3, R3.2; also elsewhere on the board
R2: K2.3, R4.2; also elsewhere on the board
R3: K4.3, R6.2; also elsewhere on the board
R4: K3.3, R5.2; also elsewhere on the board
R5: K5.3, R7.2; also elsewhere on the board
R6: K6.3, R8.2; also elsewhere on the board
R7: K7.3, R9.2; also elsewhere on the board
R8: K8.3, R10.2; also elsewhere on the board
RLY1: U3.8 (I8); also elsewhere on the board
RLY2: U3.7 (I7); also elsewhere on the board
RLY3: U3.6 (I6); also elsewhere on the board
RLY4: U3.5 (I5); also elsewhere on the board
RLY5: U3.4 (I4); also elsewhere on the board
RLY6: U3.3 (I3); also elsewhere on the board
RLY7: U3.2 (I2); also elsewhere on the board
RLY8: U3.1 (I1); also elsewhere on the board

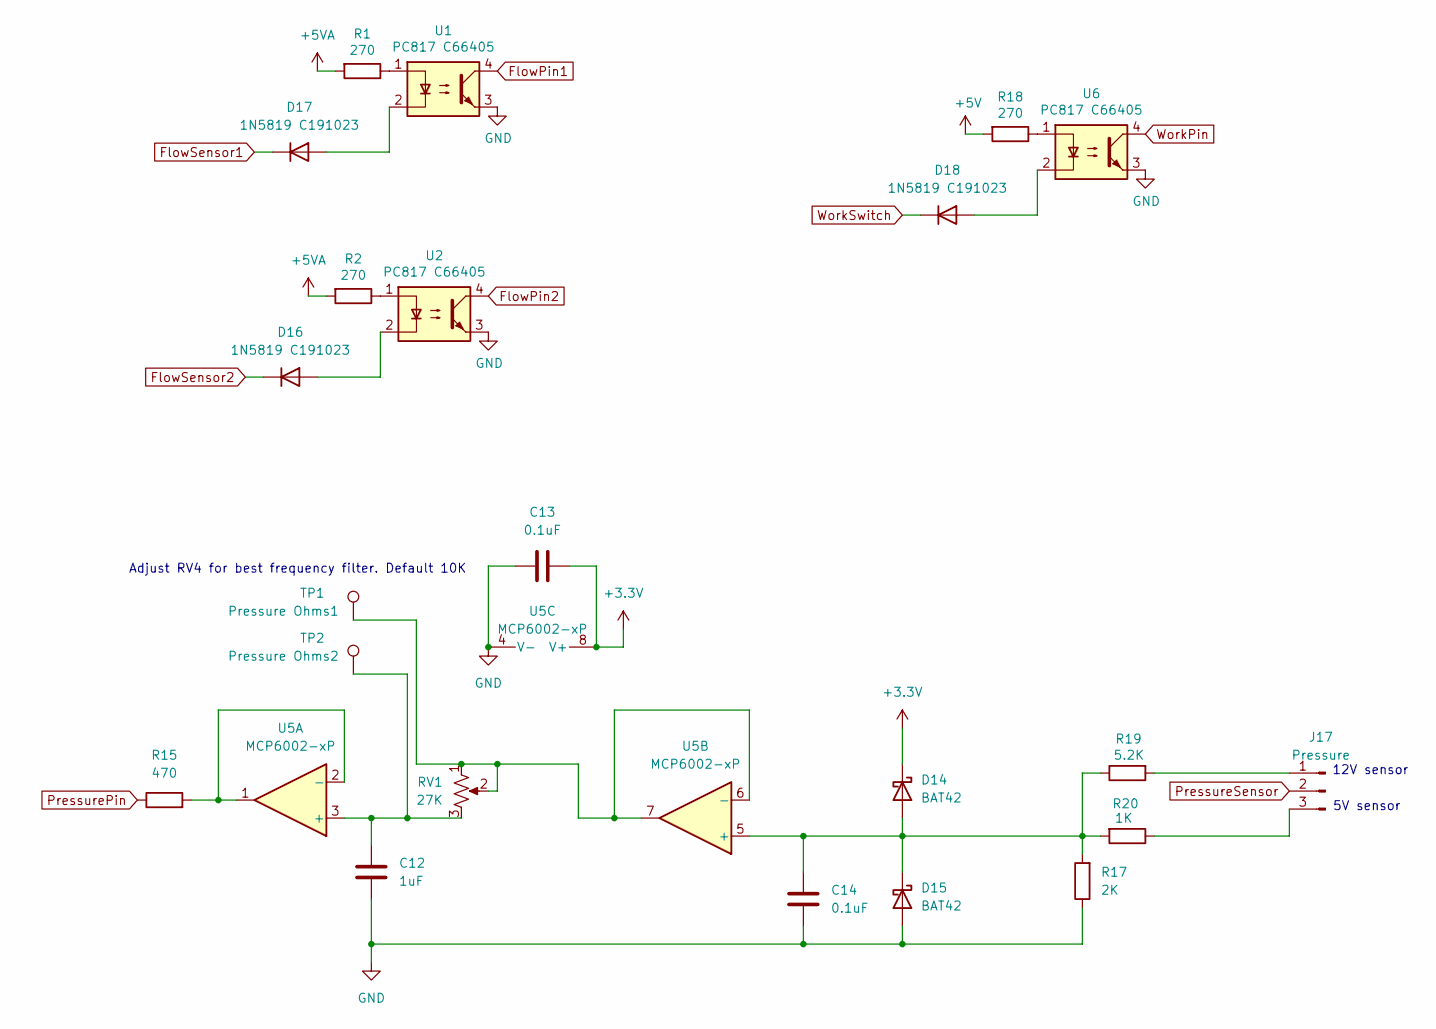
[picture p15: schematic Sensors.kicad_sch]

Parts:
C12: 1uF; C_0805_2012Metric
C13, C14: 0.1uF; C_0603_1608Metric
D14, D15: BAT42; D_SOD-123
D16, D17, D18: 1N5819 C191023; 1N5819
J17: Pressure; PinHeader_1x03_P2.54mm_Vertical
R1, R2, R18: 270; R_0603_1608Metric
R15: 470; C_0603_1608Metric
R17: 2K; R_0603_1608Metric
R19: 5.2K; R_0603_1608Metric
R20: 1K; R_0603_1608Metric
RV1: 27K; Potentiometer
TP1: Pressure Ohms1; TestPoint_THTPad_D2.5mm_Drill1.2mm
TP2: Pressure Ohms2; TestPoint_THTPad_D2.5mm_Drill1.2mm
U1, U2, U6: PC817 C66405; SMD-4_4.6x7.62mm_P2.54mm
U5: MCP6002-xP; SOIC127P600X175-8N

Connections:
+3.3V: C13.2, D14.1 (K), U5.8 (V+); also elsewhere on the board
+5V: R18.2; also elsewhere on the board
+5VA: R1.2, R2.2; also elsewhere on the board
FlowPin1: U1.4; also elsewhere on the board
FlowPin2: U2.4; also elsewhere on the board
FlowSensor1: D17.1 (K); also elsewhere on the board
FlowSensor2: D16.1 (K); also elsewhere on the board
GND: C12.2, C13.1, C14.2, D15.2 (A), R17.1, U1.3, U2.3, U5.4 (V-), U6.3; also elsewhere on the board
unnamed: C14.1, D14.2 (A), D15.1 (K), R17.2, R19.1, R20.2, U5.5 (+)
unnamed: D16.2 (A), U2.2
unnamed: D17.2 (A), U1.2
unnamed: D18.2 (A), U6.2
unnamed: J17.1, R19.2
unnamed: J17.3, R20.1
unnamed: R1.1, U1.1
unnamed: R2.1, U2.1
unnamed: R18.1, U6.1
unnamed: C12.1, RV1.3, TP2.1, U5.3 (+)
unnamed: R15.2, U5.1, U5.2 (-)
unnamed: RV1.1, RV1.2, TP1.1, U5.6 (-), U5.7
PressurePin: R15.1; also elsewhere on the board
PressureSensor: J17.2; also elsewhere on the board
WorkPin: U6.4; also elsewhere on the board
WorkSwitch: D18.1 (K); also elsewhere on the board

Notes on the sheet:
5V sensor
Adjust RV4 for best frequency filter. Default 10K
12V sensor

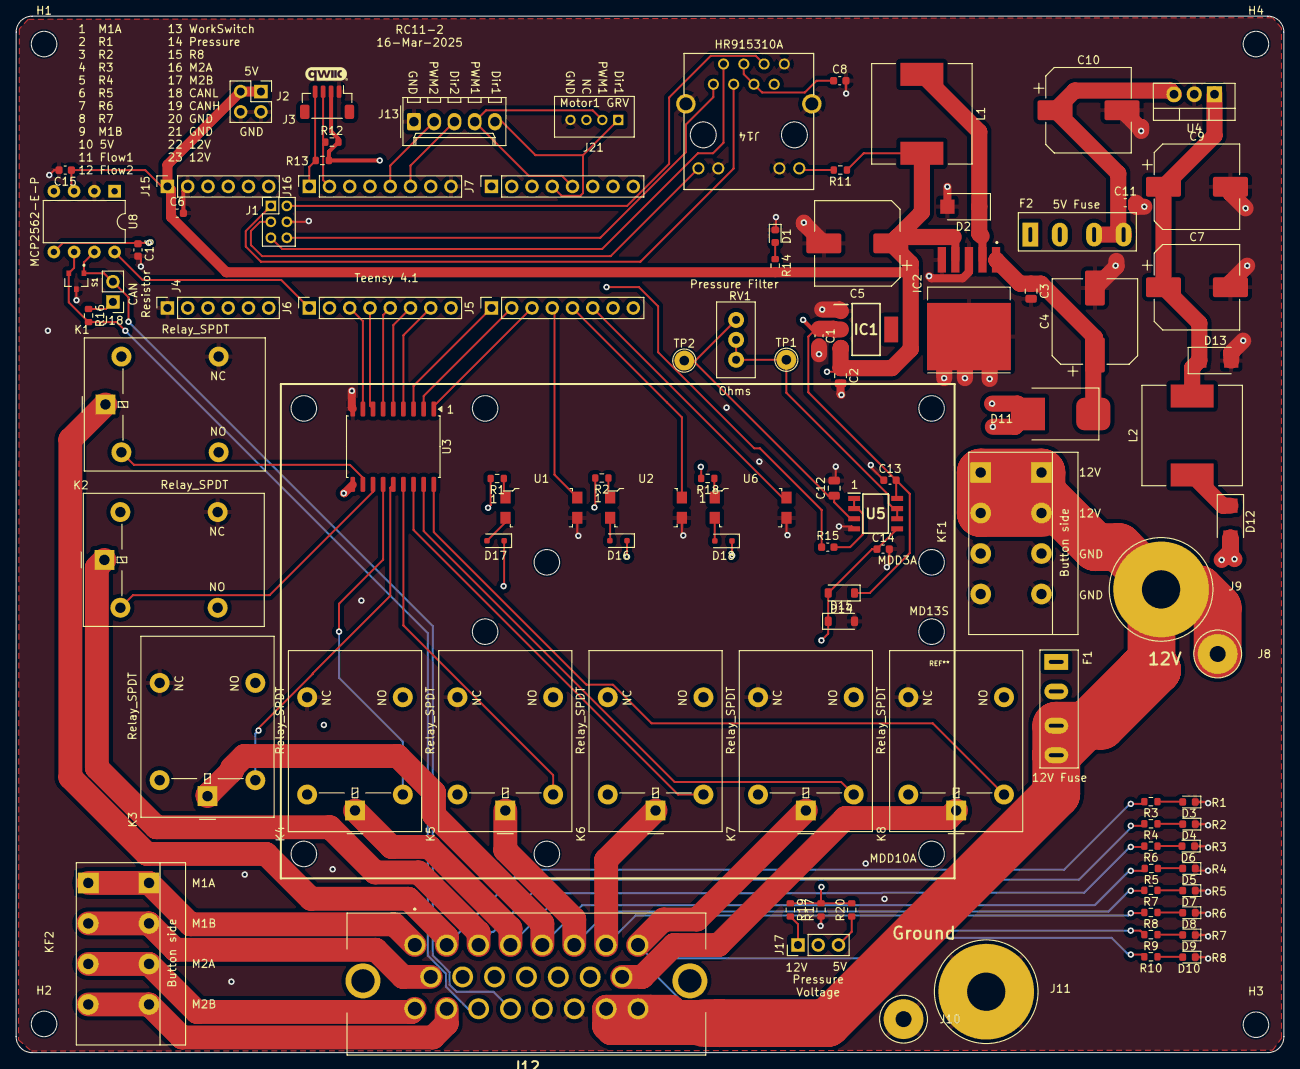
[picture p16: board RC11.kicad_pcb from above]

Board: 4 copper layers, 159.0 x 130.0 mm, 104 parts (0 on the bottom side), 87 nets.

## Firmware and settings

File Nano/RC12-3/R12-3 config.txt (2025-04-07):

7:41 AM 3/31/2025

Module ID	0
Sensor Count	2
Wifi Port	-
Relay Control	4	MCP23017	0x21
Invert Relays
Invert Flow
No Ads1115

Flow1		3
Flow2		2
Dir1		4
Dir2		6
PWM1		5
PWM2		9
Work Pin	15
Pressure	14

Relay1		0	
Relay2		15
Relay3		1
Relay4		14
Relay5		2
Relay6		13
Relay7		3
Relay8		12

Relay9		4
Relay10		11
Relay11		5
Relay12		10
Relay13		6
Relay14		9
Relay15		7
Relay16		8

no wifi

3 wire valves

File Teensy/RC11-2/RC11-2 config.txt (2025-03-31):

7:01 PM 3/29/2025

Module ID	0
Sensor Count	2
Wifi Port	-
Relay Control	GPIOs
Invert Relays
Invert Flow
No Ads1115

Flow1		28
Flow2		29
Dir1		37
Dir2		14
PWM1		36
PWM2		15
Work Pin	30
Pressure	40

Relay1		8
Relay2		9
Relay3		10
Relay4		11
Relay5		12
Relay6		25
Relay7		26
Relay8		27

no wifi

3 wire valves

CanBus		RX 23, TX 22

pinout:
1	M1A
2	R1
3	R2
4	R3
5	R4
6	R5
7	R6
8	R7
9	M1B
10	5V
11	Flow1
12	Flow2
13	Work switch
14	Pressure
15	R8
16	M2A
17	M2B
18	Can Low
19	Can High
20	GND
21	GND
22	12V
23	12V

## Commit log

2025-03-31 update RC11
    [Analog.kicad_sch, Analog.sch, BOM-RC11.csv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]
2025-04-07 update nano board
    [BOM-RC12-2.csv, BOM-RC12-2.xls, BOM-RC12-3.xls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]
